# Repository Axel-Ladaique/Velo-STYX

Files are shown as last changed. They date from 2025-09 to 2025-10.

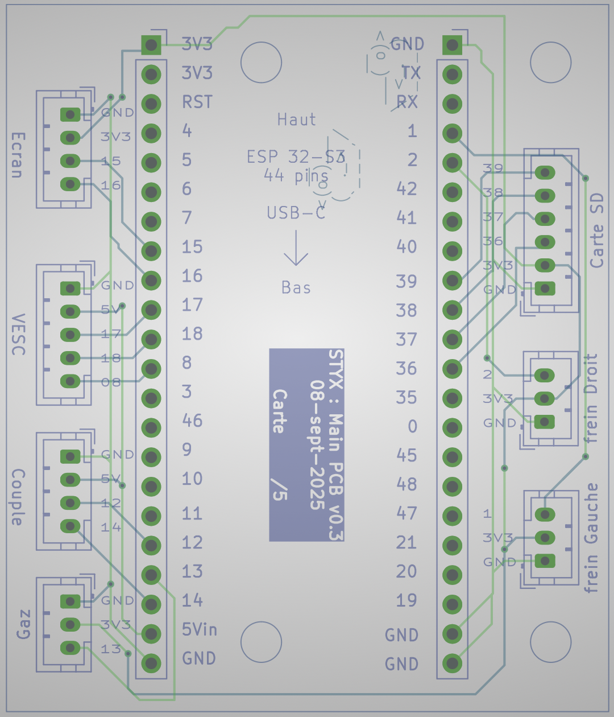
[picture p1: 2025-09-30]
05_Carte PCB/PCB_V0.3_layer_view.png

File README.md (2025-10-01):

# Velo-STYX
Codes et modèles 3D pour s'inspirer ou fabriquer le vélo styx chez soi 
## BOM : Liste des composants
Voici ci dessous la Liste des composants.

[BOM Excel (Original)](https://github.com/Axel-Ladaique/Velo-STYX/blob/main/01_BOM%20Liste%20des%20composants/1_BOM%20STYX%20V2.5.xlsx)

[BOM google sheet](https://docs.google.com/spreadsheets/d/19vOGE_QkLGgu38JTzU2YtKTNE64U9HrzXLUYEj6seYQ/edit?hl=fr&gid=0#gid=0)

Capture d’écran 2025-09-30 à 20 37 25

# Informations concernant les fichiers STEP

- Une fois l’archive décompressée, vous trouverez un fichier au format **.STEP**.  
- Ce fichier contient les modèles 3D présentés ci-dessous :
Capture d’écran 2025-09-22 à 15 25 45

# Fabrication de la carte PCB

Pour fabriquer la carte PCB, il suffit d’envoyer le fichier V0.3 (compressé en .zip) à un fabricant en ligne comme PCBWay. Une fois la commande validée, il faut régler le paiement : petit conseil, choisir la livraison lente revient beaucoup moins cher et reste fiable.
À la réception des cartes, commencez par souder les connecteurs PH2.0, puis les connecteurs JST. Une fois les soudures terminées, insérez l’ESP32 dans le sens indiqué sur la PCB, et la carte est prête à l’emploi.

Ci-dessous, la carte PCB V0.3 : vue de dessus, vue de niveau et vue de dessous.
<p align="left">
  PCB_V0 3_top_view
  PCB_V0 3_layer_view
  PCB_V0 3_bottom_view
</p>

# Marche à suivre pour la roue motorisée
Pour avoir une roue motorisée qui fonctionne avec le freinage régénératif, il nous faut un moteur particulier. Notre moteur doit être un moteur sans roue libre. Pour cela on peut opter pour un moteur direct drive (DD) ou un geared motor. 

## Moteur direct drive (ancienne version mais possible)
Pour la version direct drive, c'est plutôt simple, il suffit d'acheter un moteur direct drive intégré dans une roue arrière de vélo.  
On notera que le moteur direct drive est plus lourd et encombrant. Ce n'est pas la version retenue pour le vélo STYX v2.5 (utilisé dans le vélo STYX V1.0).  
Voici la roue que j'ai utilisée (v1.0) : [Pack Hub moteur roue arrière 26" 36V 500W](https://www.amazon.fr/dp/B0CFFTQTP3?ref=ppx_yo2ov_dt_b_product_details&th=1) 

⚠️ Cette roue est une roue 26" et n'est pas adaptée pour la V2.5 (nombre d'aimants, capteurs hall). Il faudra donc faire des modifications pour adapter une roue de ce type sur la V2.5.  
Cette roue est proposée comme une alternative à la solution geared motor.  

Ci-dessous, la roue avec moteur direct drive sur le vélo STYX V1.0 et le moteur ouvert.  
<p align="left">
  PCB_V0 3_top_view
  PCB_V0 3_layer_view
</p>

## Geared motor (Version Actuelle)
Sur la version 2.5 du vélo STYX, un moteur réducté est utilisé. Cela permet de réduire l'encombrement mais aussi et surtout le poids, c'est pour cela que la plupart des vélos électriques sur le marché sont équipés de ce type de moteur.  
Le moteur réducté est composé d'un moteur électrique entraînant un réducteur planétaire. Ce réducteur réduit la vitesse de rotation mais augmente le couple de sortie.  
Aussi, sur les vélos électriques classiques ce réducteur fait aussi office de roue libre. Cela veut dire que le moteur entraîne la roue dans un sens de rotation mais pas dans l'autre. Cela permet que le moteur entraîne la roue lorsque l'assistance est demandée, mais que lorsque la roue tourne, le moteur n'est pas entraîné. Cela augmente l'efficacité car le moteur génère une traînée électromagnétique lorsqu'il est entraîné.  
Or, dans notre système, nous ne voulons pas avoir de roue libre car notre moteur doit être entraîné par la roue pour faire du freinage régénératif. C'est pour cela que notre moteur doit être modifié par rapport aux moteurs généralement vendus dans le commerce.  

Ci-dessous, des images de porte-satellites avec et sans roue libre.  
<p align="left">
  PCB_V0 3_top_view
  PCB_V0 3_layer_view
</p>

Pour avoir un moteur réducté sans roue libre dans une roue, je suis passé par un fournisseur sur [Alibaba](https://greenpedel.en.alibaba.com/).  
Pour réduire les coûts de frais de port, j'ai commandé le moteur réducté avec la modification pour la roue libre (sans la roue) depuis la Chine puis j'ai commandé une roue motorisée sans modification envoyée depuis l'Europe.  
J'ai fait cette manipulation car je voulais essayer le moteur sans la roue avant de commander le tout avec la roue.  

Voici les prix des différentes options :  

#### Option 1 (testé) :  
  Achat en 2 commandes puis assemblage de la partie modifiée dans la roue (assemblage très simple). Voir les 2 commandes dans [PI fournisseur](https://github.com/Axel-Ladaique/Velo-STYX/tree/main/01_BOM%20Liste%20des%20composants/PI_Fournisseur)  
  + Moteur modifié envoyé de Chine = $45 + $88 = $133 (produit + frais de port = total) [Voir facture moteur](https://github.com/Axel-Ladaique/Velo-STYX/blob/main/01_BOM%20Liste%20des%20composants/PI_Fournisseur/PI_Moteur.pdf)  
  + Roue motorisée (envoyée d'Europe) = $189 (produit + frais de port = total) [Voir facture roue](https://github.com/Axel-Ladaique/Velo-STYX/blob/main/01_BOM%20Liste%20des%20composants/PI_Fournisseur/PI_Moteur.pdf)  
  + Total avec FDP = $322  

  Pour rendre le moteur avec la roue compatible avec la regen, il suffit d'ouvrir le moteur modifié (sans roue), d'en sortir le moyeu moteur (voir photo ci-dessous) et de remplacer le moyeu de la roue motorisée par le moyeu modifié.  
  <p align="left">
    PCB_V0 3_top_view
    PCB_V0 3_layer_view
  </p>

#### Option 2 (pas testée) :  
  Achat en 1 commande (pas testé mais même fournisseur donc mêmes composants)  
  + Moteur modifié avec roue assemblée : $55 + $229 = $284  

#### Option 3 (pas testée) :  
  Achat en 1 commande du moteur modifié  
  + Moteur modifié envoyé de Chine = $45 + $88 = $133 (produit + frais de port = total)  
  + Rayons et jante adaptés (prix = ?)  
  + Assemblage de la roue chez un atelier de vélo local (prix = ?)  

#### Option 4 (pas testée) :  
  Achat en 1 commande de la roue avec le moteur non modifié puis modification du porte-satellite [Voir facture](https://github.com/Axel-Ladaique/Velo-STYX/blob/main/01_BOM%20Liste%20des%20composants/PI_Fournisseur/PI_Roue.pdf)  
  + Roue motorisée avec moteur non modifié : $189 (produit + frais de port = total)  
  + Modification du porte-satellite avec poste à souder [vidéo](https://youtu.be/KDuZFQy_Q-I?si=F1o1J4BLGezd9nKO)

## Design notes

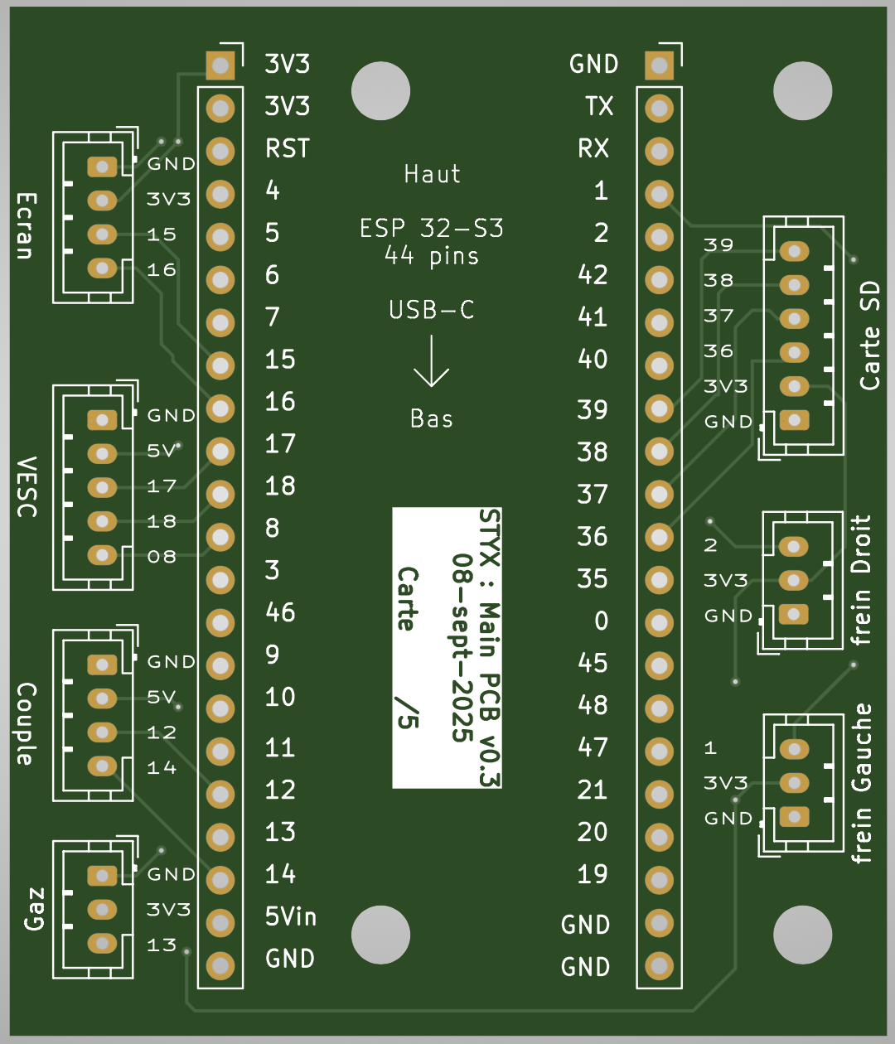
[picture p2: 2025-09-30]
05_Carte PCB/PCB_V0.3_top_view.png

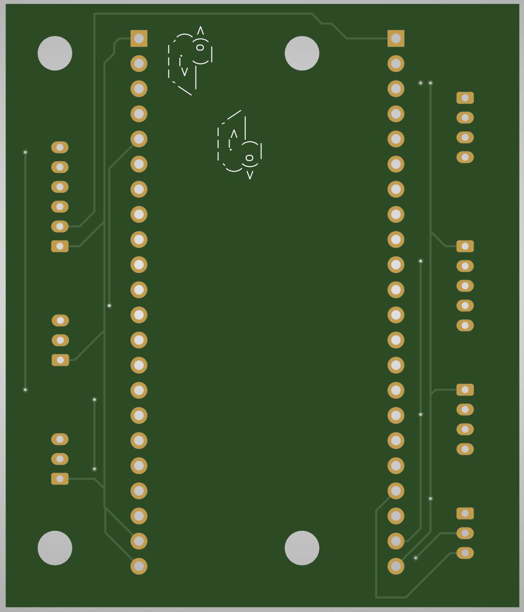
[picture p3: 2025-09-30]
05_Carte PCB/PCB_V0.3_bottom_view.png

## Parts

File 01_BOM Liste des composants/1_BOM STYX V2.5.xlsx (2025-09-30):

Sous système | Item | Commentaire | Lien | Qté | prix unitaire | Total
Vélo STYX complet |  |  |  |  |  | 1560.17 €
Vélo base |  |  |  |  |  | 567.89 € | Sous système | Item | Commentaire | Lien | Qté | prix unitaire | Total
 | TRIBAN RC500 FLATBAR PROWHEEL / SORA | Le vélo doit avoir des frein a disque mecanique (pas d'hydraulique) et un guidon plat | decathlon (https://www.decathlon.fr/p/triban-rc500-flatbar-prowheel-sora/_/R-p-345067) | 1 | 549.00 € | 549.00 € | Outils utiles |  |  |  |  |  | 83.77 €
 | Roue libre PNA 8 vitesses 13/28 | /!\ Roue libre 8 vitesse pour Selecteur 9 vitesse | Beasty-bike (https://www.beastybike.com/cassettes-roues-libres/10396-roue-libre-pna-8-vitesses-13-28.html) | 1 | 18.89 € | 18.89 € |  | Pince à sertir borne à ressort enfichable DuPont SN-2549 | Pour PH2.0 | aliexpress (https://fr.aliexpress.com/item/1005007269635511.html) | 1 | 9.99 € | 9.99 €
Moteur/Roue |  |  |  |  |  | 371.47 € |  | Pince à sertir SN-6 JAW | Pour terminaux UT4-5 | aliexpress (https://fr.aliexpress.com/item/1005008593957205.html) | 1 | 3.79 € | 3.79 €
 | GP-G24R Regen motor only | Moteur avec regen seul (sans la roue) || voir PI pour details | greenpedel-alibaba (https://greenpedel.en.alibaba.com/) | 1 | / | 149.04 € |  | BOITE A OUTILS VELO 900 |  | Decathlon (https://www.decathlon.fr/p/boite-a-outils-velo-900/_/R-p-100427?mc=8381080) | 1 | 69.99 € | 69.99 €
 | GP-G24R Motor-Wheel kit | Moteur sans regen integré dans la roue || voir PI pour details | greenpedel-alibaba (https://greenpedel.en.alibaba.com/) | 1 | / | 207.84 €
 | Câble d'extension de moteur de moyeu Ebike Julet 9 broches (60cm female) |  | aliexpress (https://fr.aliexpress.com/item/1005003749778364.html) | 1 | 14.59 € | 14.59 €
Capteur de couple |  |  |  |  |  | 143.86 € | Plastique pour impression |  |  |  |  |  | 110.96 €
 | Capteur de couple | voir PI pour details | greenpedel-alibaba (https://greenpedel.en.alibaba.com/) | 1 | / | 141.55 € |  | TPU for AMS |  | bambulab (https://eu.store.bambulab.com/fr/products/tpu-for-ams) | 1 | 39.99 € | 39.99 €
 | Connecteur étanche Julet Higo (6 pin Female) |  | aliexpress (https://fr.aliexpress.com/item/1005006444582628.html?gatewayAdapt=glo2fra) | 1 | 2.31 € | 2.31 € |  | ASA |  | bambulab (https://eu.store.bambulab.com/fr/products/asa-filament) | 1 | 24.99 € | 24.99 €
Levier de frein |  |  |  |  |  | 39.58 € |  | PLA Matte |  | bambulab (https://eu.store.bambulab.com/fr/products/pla-matte?id=42996742652123) | 2 | 22.99 € | 45.98 €
 | Ebrake Levers with Analog Output, Left | Envoyé depuis de canada (fraits de port élevés) | ebikes.ca (https://ebikes.ca/ebrake-analog-higo4-left-ls.html) | 1 | 18.00 € | 18.00 €
 | Ebrake Levers with Analog Output, Right | Envoyé depuis de canada (fraits de port élevés) | ebikes.ca (https://ebikes.ca/ebrake-analog-higo4-right.html) | 1 | 18.00 € | 18.00 €
 | Connecteur étanche Julet Higo (4 pin Female) |  | aliexpress (https://fr.aliexpress.com/item/1005006444582628.html?gatewayAdapt=glo2fra) | 2 | 1.79 € | 3.58 €
Ecran GPS |  |  |  |  |  | 45.78 €
 | ESP32 S3 Screen |  | aliexpress (https://fr.aliexpress.com/item/1005006211756061.html) | 1 | 23.39 € | 23.39 €
 | Module GPS |  | aliexpress (https://fr.aliexpress.com/item/1005006494891194.html) | 1 | 19.79 € | 19.79 €
 | Insert M2.5(OD3.5mm)x2.5mm 50pcs | Attention M2.5 (pas M3) | aliexpress (https://fr.aliexpress.com/item/1005003582355741.html) | 1 | 1.66 € | 1.66 €
 | Vis, Class steel, M2.5x4mm 50pcs | Attention M2.5 (pas M3) | aliexpress (https://fr.aliexpress.com/item/32810872544.html) | 1 | 0.94 € | 0.94 €
Pack de condo |  |  |  |  |  | 246.02 €
 | Cellule ultracondensateur 700F 2,7V (interface 2xM5) |  | capcomp (https://shop24.capcomp.de/en/capacitors/ultracap/cells/500f-to-2999f/1123/ultracap-zelle-700f-2-7v-innengewinde-2xm5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) | 20 | 8.89 € | 200.84 €
 | Terminaux cosses à fourche UT4-5 (50 pcs) | besoin de Pince à sertir SN-6 JAW | aliexpress (https://fr.aliexpress.com/item/1005007812607726.html) | 2 | 2.85 € | 5.70 €
 | Carte d'équilibrage de supercondensateur 35mm (2,7V) |  | aliexpress (https://fr.aliexpress.com/item/1005008858296510.html) | 20 | 1.56 € | 31.20 €
 | Stainless Steel, M5 10pcs, 6mm |  | aliexpress (https://fr.aliexpress.com/item/32810872544.html) | 6 | 1.38 € | 8.28 €
Electronique de puissance |  |  |  |  |  | 114.44 €
 | Interupteur 40A |  | aliexpress (https://fr.aliexpress.com/item/1005006290676888.html?curPageLogUid=gCNnFQmCMfqb) | 1 | 1.44 € | 1.44 €
 | FLIPSKY Mini V6 MK5 With Power Button |  | flipsky.net (https://flipsky.net/collections/v6-series/products/mini-v6-mk5-with-power-button) | 1 | 100.00 € | 100.00 €
 | Insert flités M3(OD5) x 5mm | Attention M5 (pas M3) | aliexpress (https://fr.aliexpress.com/item/1005003582355741.html) | 1 | 1.99 € | 1.99 €
 | Câble en Silicone rouge et noir 12AWG (3m) |  | aliexpress (https://fr.aliexpress.com/item/1005007356973020.html) | 1 | 8.99 € | 8.99 €
 | Adaptateur de données mâle vers micro USB femelle à angle droit (V8DO-V8F) |  | aliexpress (https://fr.aliexpress.com/item/1005006553808623.html) | 1 | 2.02 € | 2.02 €
Electronique analyse |  |  |  |  |  | 31.13 €
 | Carte de développement double Type C ESP32-S3 (N16R8 weld) |  | aliexpress (https://fr.aliexpress.com/item/1005005051294262.html) | 1 | 5.39 € | 5.39 €
 | Adaptateur USB C mâle vers femelle, Extension à 90 degrés, 85DD |  | aliexpress (https://fr.aliexpress.com/item/1005004503201824.html) | 1 | 1.29 € | 1.29 €
 | Bande de connecteur JST | Fichier de fabrication en .zip | aliexpress (https://fr.aliexpress.com/item/4000873858801.html) | 1 | 1.69 € | 1.69 €
 | Impression PCB |  | pcbway (https://www.pcbway.fr/) | 1 | 10.00 € | 10.00 €
 | PH2.0 | a verifier | amazon (https://www.amazon.fr/Lyeteung-Connecteur-Broches-Femelle-Pré-Sertis/dp/B0CDG95RDT?__mk_fr_FR=ÅMÅŽÕÑ) | 1 | 11.99 € | 11.99 €
 | Micro SD Card Mini TF Card Reader (Mini SD Card) (https://www.aliexpress.com/item/3256806062285034.html) |  | aliexpress (https://fr.aliexpress.com/item/1005006248599786.html) | 1 | 0.77 € | 0.77 €
Visserie & autres
 | Manchon de câble tressé (5M, Inner Diameter 8mm) |  | aliexpress (https://fr.aliexpress.com/item/1005006219473493.html) | 1 | 4.89 € | 4.89 €
 | Vis, Class steel, M3 | Nombre de vis et hauteur à definir | aliexpress (https://fr.aliexpress.com/item/1005008585550992.html) | 5 | 2.20 € | 11.00 €
 | Insert M3(OD5mm) | Nombre d'insert et hauteur à definir | aliexpress (https://fr.aliexpress.com/item/1005003582355741.html) | 2 | 1.50 € | 3.00 €

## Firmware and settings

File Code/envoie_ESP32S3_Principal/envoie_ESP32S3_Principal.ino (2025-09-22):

/* CODE TEST 20/09/2025 19h15 => Main PCB Envoie Json ESP32S3 --> écran.  échange info Vesc <--> esp32S3 (Main PCB)
//!\\ PCB V0.3
//21/09 Ajout du capteur de cadence
//20/09 Passage en PCB V0.3, changement de pin et lecture du capteur de couple
//13/08 Fix distance + Ajout d’un variateur pour le freinage regeneratif. Test de ralentir automatiquement au dessus de 25km peu concluant
//23/07/2025 Si un fichier existe, creation d'un nouveau fichier pour ne pas ecraser le ficher precedent sur la carte SD 
//20/07/25 Enregistrement des données envoyés par le GPS/ecran. 
//21/06 remise a plat apres les test en I2c et bluetooth car ca ne marchait pas on va ensuite tester de metre le gps sur l’écran.
 Validation => récupère les données du VESC et les envoie sur l’écran. 
 Si le VESC est débranché, envoie des données aléatoires.
 Si VESC rebranché, les données reviennent sur l’écran.

 Validation 2. Recuperation de la valeur du frein et de la gachette des gaz avec envoie sur l'ecran.
 Validation 3 : envoie de la commande au vesc : tunes a revoir mais frein et acceerateur fonctionnent
 22/01 19h30 => Fix distance & vitesse 
 25/01 12h50 => re fix distance, fix calcul d’envoie au vesc 
 25/01 14h40 => changement de la vitesse du serial screen en 115200 Bauds, optimisation du temps d'exectuion de la loop.
 01/02 17h30 => changement sur les envoie de donné au vesc, probleme de multiplicateur réglé.
 07/02 Fix Ah charged/discharged ==> Wh charged Discharged. || fix distance facteur 12,1

Modification du 09/05/2025 pour la nouvelle roue. Changement diamètre, nb poles pour vitesse, 

/* Code écrit par Axel LADAIQUE */
/* Ce code a pour but de traiter et d'envoyer les informations du vélo STYX sur un écran de dev avec ESP32 S3 et une carte SD

Configuration Board => 
- Esp32S3 dev module
- Port Serial (voir problème port/driver)
- Flash Size : 16MB
- Partition scheme : 8M with SPIFF ...
- PSRAM : disable

/ ! \ Arduino IDE v2.3.2 || TFT_eSPI v2.5.43 || esp32 by Espressif v2.0.12
*/

#include <ArduinoJson.h>
#include <HardwareSerial.h>
#include <VescUart.h>

// UART pour la communication avec l'écran
HardwareSerial SerialScreen(1); // UART1 pour l'écran
#define TX_PIN_SCREEN 15 // Pin TX vers le récepteur (écran)
#define RX_PIN_SCREEN 16 // Pin RX (non utilisé ici)

// UART pour la communication avec le VESC
HardwareSerial SerialVESC(2); // UART2 pour le VESC
VescUart vesc; // Objet pour la bibliothèque VESC
#define TX_PIN_VESC 17 // Pin TX pour le VESC
#define RX_PIN_VESC 18 // Pin RX pour le VESC

// Pins supplémentaires pour alimentation et lecture analogique
#define PIN_FREIN_DROIT 2
#define PIN_FREIN_GAUCHE 1
#define PIN_GAZ 13
const int freinInf = 1050;
const int freinSup = 2500;
const int freinInf_G = freinInf;
const int freinSup_G = freinSup;
const int freinInf_D = freinInf;
const int freinSup_D = freinSup;

const int gazInf = 985;
const int gazSup = 3125;


#include <SD.h>
#include <SPI.h>
// Déclaration des pins SPI personnalisées
#define CS_PIN_SD 39
#define MOSI_PIN 38
#define MISO_PIN 36
#define CLK_PIN 37
File dataFile;

#define PIN_COUPLE 12
#define PIN_CANDENCE 14

volatile unsigned long lastPulseMicros = 0;
volatile unsigned long pulseIntervalMicros = 0;
volatile unsigned long pulseCountCad = 0;

float cadenceRPM = 0.0;
const int pulsesPerRevCad = 36;  // nombre d'impulsions par tour (1 aimant = 1 impulsion)
#define WINDOW_MS 500         // Fenêtre pour moyenne glissante
#define TIMEOUT_MS 300        // Timeout sans impulsion pour remettre cadence à 0
#define ALPHA 0.3             // Filtrage exponentiel

float cadenceFiltered = 0;     // Valeur moyenne lissée
unsigned long lastCadenceUpdate = 0;
volatile unsigned long lastPulseTime = 0; // mis à jour dans l'ISR


bool rec = false;
String currentFilename;

String generateUniqueFilename() {
  String baseFilename = "/STYXvelo_P2_AL";
  String extension = ".csv";
  String filename;
  int counter = 1;
  
  // Vérifier si le fichier de base existe
  filename = baseFilename + extension;
  if (!SD.exists(filename)) {
    return filename; // Le fichier de base n'existe pas, on peut l'utiliser
  }
  
  // Chercher un nom de fichier libre avec un numéro
  do {
    filename = baseFilename + "_" + String(counter) + extension;
    counter++;
  } while (SD.exists(filename) && counter < 1000); // Protection contre boucle infinie
  
  return filename;
}

void IRAM_ATTR isr_cadence() {
  unsigned long now = micros();
  unsigned long interval = now - lastPulseMicros;
  if (interval > 20000) { // ignore <20ms (anti-rebond)
    pulseIntervalMicros = interval;
    pulseCountCad++;
    lastPulseMicros = now;
    lastPulseTime = millis(); // <- pour le timeout
  }
}




void setup() {
  // Initialisation des UART
  SerialScreen.begin(115200, SERIAL_8N1, RX_PIN_SCREEN, TX_PIN_SCREEN);
  SerialVESC.begin(115200, SERIAL_8N1, RX_PIN_VESC, TX_PIN_VESC);

  // Association explicite du port série avec l'objet VESC
  vesc.setSerialPort(&SerialVESC);

  // Moniteur série pour le débogage
  Serial.begin(115200);
  delay(1000);



  // Configuration des pins de frein, gaz et couple pour lecture analogique
  pinMode(PIN_FREIN_GAUCHE, INPUT);
  pinMode(PIN_FREIN_DROIT, INPUT);
  pinMode(PIN_GAZ, INPUT);
  pinMode(PIN_COUPLE, INPUT);
  pinMode(PIN_CANDENCE, INPUT_PULLUP);
  attachInterrupt(digitalPinToInterrupt(PIN_CANDENCE), isr_cadence, FALLING);
  analogReadResolution(12);           // Résolution ADC : 12 bits
  analogSetAttenuation(ADC_11db);     // Plage de lecture : 0 à 3.3V

  Serial.println("Émetteur prêt avec :");
  Serial.println("- UART1 : TX=15, RX=16 pour le récepteur (écran)");
  Serial.println("- UART2 : TX=17, RX=18 pour le VESC");

  
  SPI.begin(CLK_PIN, MISO_PIN, MOSI_PIN, CS_PIN_SD);
  // Initialisation de la carte SD
  if (!SD.begin(CS_PIN_SD, SPI)) {
    Serial.println("Erreur : Impossible d'initialiser la carte SD !");
    //while (true);
  }
  Serial.println("Carte SD initialisée avec succès.");

  // Générer un nom de fichier unique
  currentFilename = generateUniqueFilename();
  Serial.println("Nom du fichier : " + currentFilename);
  
  // Ouvrir le fichier pour écriture (crée un nouveau fichier)
  dataFile = SD.open(currentFilename, FILE_WRITE);
  if (dataFile) {
    // Écriture des en-têtes
    dataFile.println("Temps,Tension,Vitesse,GazFrein,WHCharged,WHDischarged,Distance,CurrentIn,MotorCurrent,Lat,Lon,Alt,Vsat,Cap,Sat,HDOP,Heure,Date,Couple,CadenceRPM");
    rec = true;
    dataFile.close();
  } else {
    Serial.println("Erreur : Impossible de créer le fichier " + currentFilename + " !");
    rec = false;
  }

}

float coef_couple = 1.0;
float current_motor;
int lastsd_MS=0;
float vari_vesc = 0;
int nb = 0;
float couple_moy =0;

void loop() {
  int millisdeb = millis();
  nb = nb+1;

  // Lecture des valeurs analogiques
  int frein_G = analogRead(PIN_FREIN_GAUCHE);
  int frein_D = analogRead(PIN_FREIN_DROIT);
  //Serial.print("Valeur frein_G Brute (pin 19) : ");
  //Serial.println(frein_G);
  frein_G = map(frein_G, freinInf_G, freinSup_G, 0, -90);
  //Serial.print("Valeur frein_D Brute (pin 12) : ");
  //Serial.println(frein_D);
  frein_D = map(frein_D, freinInf_D, freinSup_D, 0, -90);
  int frein = frein_G + frein_D;
  if (frein < -90) {frein = -90;}

  int gaz = analogRead(PIN_GAZ);
  //Serial.print("Valeur gaz (pin 20) : ");
  //Serial.println(gaz);
  gaz = map(gaz, gazInf, gazSup, 0, 90);
  float couple = analogRead(PIN_COUPLE);
  Serial.print("couple brut : " );
  Serial.print(couple);
  couple = 0.0267*couple-22.948;
  if (couple<0){
    couple = 0;
  }
  //float cadence = cadenceRPM;
  Serial.print("||  couple : " );
  Serial.print(couple);
  Serial.print(" Nm    nb : " );
  Serial.print(nb);
  couple_moy = (couple_moy+couple);
  Serial.print("   || couple_moy : " );
  Serial.print(couple_moy/nb);
  // Calcul cadence (RPM)
  unsigned long now = millis();
  // Calcul toutes les WINDOW_MS
  if (now - lastCadenceUpdate >= WINDOW_MS) {
      lastCadenceUpdate = now;

      noInterrupts();
      unsigned long pulses = pulseCountCad;   // nombre d’impulsions dans la fenêtre
      pulseCountCad = 0;                       // remise à zéro
      interrupts();

      float cadenceRPM = 0.0;
      if (pulses > 0) {
          float revPerSec = (float)pulses / (float)pulsesPerRevCad / (WINDOW_MS / 1000.0);
          cadenceRPM = revPerSec * 60.0;
      }

      // Timeout si plus d’impulsion depuis TIMEOUT_MS
      if (now - lastPulseTime > TIMEOUT_MS) {
          cadenceRPM = 0.0;
      }

      // Filtrage exponentiel pour lisser
      cadenceFiltered = (1 - ALPHA) * cadenceFiltered + ALPHA * cadenceRPM;

      Serial.print("Cadence filtrée (RPM) : ");
      Serial.println(cadenceFiltered);
  }
  //delay(1000);
  // Affichage des valeurs analogiques
  /*Serial.print("Valeur frein (pin 12) : ");
  Serial.println(frein);
  Serial.print("Valeur gaz (pin 14) : ");
  Serial.println(gaz);*/
  float gazfrein = 0;
  if (gaz>90){gaz=90;}
  
  if (frein<0) {gazfrein=frein;}
  else {
    if (gaz <0){gazfrein=0;}
    else{gazfrein=gaz;}
  }

  //Serial.println( "temps gazfrein : " + String (millis() - millisdeb));
  //Serial.print("Valeur gazFREIN : ");
  //Serial.println(gazfrein);

  // Préparation des données JSON
  StaticJsonDocument<500> doc;

  doc["Gaz/frein"] = gazfrein;
  doc["Temps seconde"] = millis() / 1000.0;

  float vitesse = 0;

  if (vesc.getVescValues()) {
    // Lecture des valeurs du VESC
    //Serial.println("Vesc");
    doc["Tension"] = vesc.data.inpVoltage;
    float rpm = vesc.data.rpm/10;                         // The ’10’ is the number of pole pairs in the motor. the motors have 52 poles, therefore 26 pole pairs
    vitesse = rpm*60*PI*(28*0.0254)/(1000)/4.4;       //vitesse en Km/h
    //Serial.println("RPM :" + String(rpm) + "vitesse :" + String(vitesse));
    doc["Vitesse"] = vitesse; // Convertir RPM en vitesse
    doc["WHcharged"] = vesc.data.wattHoursCharged;
    doc["WHdischarged"] = vesc.data.wattHours;
    float tach = vesc.data.tachometer/(20*3);           // The '52' is the number of motor poles multiplied by 3 (3hall sensor I think)
    //Serial.println ("tach : " + String(tach));
    float distance = tach*3.142*(0.001)*(28.0*0.0254)/4.4;       // 3.142*(0.0001)*(26.0*0.0254) //26*0.0254 = diametre de la roue (26 pouces *0,0254). Je ne sais pas pk *12.1
    doc["Distance"] = distance;
    //Serial.println ("Disatnce : " + String(distance));
    doc["Current_in"] = vesc.data.avgInputCurrent;
    doc["Message"] = "VESC_OK";
  } else {
    Serial.println("pas vesc");
    doc["Tension"] = 99.99;
    doc["Vitesse"] = 99.9; // Convertir RPM en vitesse
    doc["WHcharged"] = 99.99;
    doc["WHdischarged"] = 99.99;
    doc["Distance"] = 999.99;
    doc["Current_in"] = 99.99;
    // En cas d'échec de lecture du VESC
    doc["Message"] = "VESC_NOK";
  }
  current_motor=vesc.data.avgMotorCurrent;
  doc["Rec"] = rec;
  //Serial.println("doc Rec" + String(rec));
  // Sérialisation des données JSON
  String jsonOutput;
  serializeJson(doc, jsonOutput);

  //Serial.println( "temps json+infovesc : " + String (millis() - millisdeb));

  // Envoi des données JSON via UART (écran)
  SerialScreen.println(jsonOutput);
  //Serial.println("Longueur de jsonOutput : " + String(jsonOutput.length()));

  //Serial.println( "temps send ecran : " + String (millis() - millisdeb));

  // Affichage pour le débogage
  //Serial.println("Données envoyées :");
  //Serial.println(jsonOutput);

  // Enregistrer les données dans un fichier CSV
  if (vesc.getVescValues()) {
    if (millis()-lastsd_MS>500){
      if (rec==true){
      
        Serial.println("if milis + rec ");
        if (SerialScreen.available()) {
          Serial.println("serial screen");
          // Lecture de la chaîne JSON envoyée
          String receivedData = SerialScreen.readStringUntil('\n');
          receivedData.trim(); // Supprime les espaces ou retours à la ligne en début et fin de chaîne

          // Affiche la chaîne brute reçue pour débogage
          Serial.print("Données reçues brutes : ");
          Serial.println(receivedData);

          // Parse le JSON reçu
          StaticJsonDocument<256> doc_gps;
          DeserializationError error = deserializeJson(doc_gps, receivedData);

          if (error) {
            Serial.print(F("Erreur de parsing JSON: "));
            Serial.println(error.c_str());
            return;
          }

          // Récupérer les champs du JSON GPS
          float latitude     = doc_gps["lat"];       // Latitude (Float)
          float longitude    = doc_gps["lon"];     // Longitude (Float)
          float altitude     = doc_gps["alt"];     // Altitude (Float)
          float vitesse_sat  = doc_gps["spd"];     // Vitesse satellite (Float)
          float cap          = doc_gps["hdg"];     // Cap (Float)
          int satellites     = doc_gps["sat"];     // Nombre de satellites (Int)
          float hdop         = doc_gps["hdop"];    // Précision horizontale (Float)
          unsigned long heure_GMT = doc_gps["tim"]; // Heure brute GMT (ULong)
          unsigned long date       = doc_gps["dat"]; // Date brute (ULong)

          // Affichage des données GPS pour débogage
          Serial.println("Données GPS reçues et parsées :");
          Serial.print("Latitude : "); Serial.println(latitude, 6);
          Serial.print("Longitude : "); Serial.println(longitude, 6);
          Serial.print("Altitude (m) : "); Serial.println(altitude);
          Serial.print("Vitesse satellite (km/h) : "); Serial.println(vitesse_sat);
          Serial.print("Cap (°) : "); Serial.println(cap);
          Serial.print("Satellites : "); Serial.println(satellites);
          Serial.print("HDOP : "); Serial.println(hdop);
          Serial.print("Heure GMT brute : "); Serial.println(heure_GMT);
          Serial.print("Date brute : "); Serial.println(date);

          dataFile = SD.open(currentFilename, FILE_APPEND);
          if (dataFile) {
            rec=true;
            dataFile.print(doc["Temps seconde"].as<float>());
            dataFile.print(",");
            dataFile.print(doc["Tension"].as<float>());
            dataFile.print(",");
            dataFile.print(doc["Vitesse"].as<float>());
            dataFile.print(",");
            dataFile.print(doc["Gaz/frein"].as<float>());
            dataFile.print(",");
            dataFile.print(doc["WHcharged"].as<float>());
            dataFile.print(",");
            dataFile.print(doc["WHdischarged"].as<float>());
            dataFile.print(",");
            dataFile.print(doc["Distance"].as<float>());
            dataFile.print(",");
            dataFile.print(doc["Current_in"].as<float>());
            dataFile.print(",");
            dataFile.print(current_motor);
            dataFile.print(",");
            dataFile.print(doc_gps["lat"].as<float>(),6);
            dataFile.print(",");
            dataFile.print(doc_gps["lon"].as<float>(),6);
            dataFile.print(",");
            dataFile.print(doc_gps["alt"].as<float>());
            dataFile.print(",");
            dataFile.print(doc_gps["spd"].as<float>());
            dataFile.print(",");
            dataFile.print(doc_gps["hdg"].as<float>());
            dataFile.print(",");
            dataFile.print(doc_gps["sat"].as<int>());
            dataFile.print(",");
            dataFile.print(doc_gps["hdop"].as<float>());
            dataFile.print(",");
            dataFile.print(doc_gps["tim"].as<unsigned long>());
            dataFile.print(",");
            dataFile.print(doc_gps["dat"].as<unsigned long>());
            dataFile.print(",");
            dataFile.print(couple_moy/nb);
            dataFile.print(",");
            dataFile.println(cadenceFiltered);
            dataFile.close();
          } else {
            rec=false;
          //Serial.println("Erreur : Impossible d'écrire dans le fichier datalog.csv !");
          } 
        }
      } 
      nb = 0;
      couple_moy =0;
      lastsd_MS=millis();
    }
  }

    //Serial.println( "temps sd : " + String (millis() - millisdeb));
  //-------------------------------------------------------------------------------------------
  //Envoie de données au Vesc 
  float comVesc = 0;
  comVesc = gazfrein/90;  //remet entre -1 et 1
  
  //Serial.println("comVesc avant : " + String(comVesc));
  //Serial.println("comvesc" + String(comVesc));
  if (comVesc<-0.1){
    if (vari_vesc>(comVesc*25)){
      vari_vesc = vari_vesc - 0.4;  
    }else{
      vari_vesc=comVesc*25;
    }
    vesc.setBrakeCurrent(vari_vesc); // entre 0 et -25A
  }
  Serial.print("vari_vesc : ");
  Serial.println(vari_vesc);
  Serial.print("comvesc *25 : ");
  Serial.println(comVesc*25);

  if (comVesc>0.1){
    vari_vesc = 0;
    comVesc=comVesc*15;
    vesc.setCurrent(comVesc);        //entre 0 et 20A
    
  }
  if (vitesse>25){
    vesc.setRPM(820); //820 RPM <=> 25 km/h
    Serial.print("au dessus de 25km/h : ");
    Serial.println(vitesse);
    comVesc=0;
  }
  if (comVesc>-0.1 && comVesc<0.1){ 
    comVesc=0; 
    vari_vesc = 0;
    vesc.setCurrent(comVesc);
  }

  //Serial.println( "temps fin : " + String (millis() - millisdeb));
  
  //Serial.println("comVesc apres : " + String(comVesc));
  


  //-------------------------------------------------------------------------------------------


  //delay(40); // Pause avant prochaine boucle
  //delay(2000);
}

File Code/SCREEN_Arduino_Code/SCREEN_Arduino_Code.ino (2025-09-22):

//CODE FONTIONEL 20/07 16h30 => Affichage sur ecran + réception Json ESP32S3
//20/07 Fix transmission/Enregistrement des données GPS. Fix affichage vitesse et attfichage début.
//16/07 ajout du gps A essayer avec le reste du vélo (verifier l'envoie des données gps lors de l'envoie/reception de la commande message = "____GPS")
//21/06 remise a plat apres les test I2C et bleutooth car ca ne fonctionne pas. 
// 16_16/03 16h40 ===> correction aute orthographe + 1pxl jauges
//fix de la jauge de droite (mtn dans le bon sens)
//Ajout page de demarrage 
//fix distance et rec
//Fix serial 115200
//preparation touch screen (touch screen ready
//toucher pour passer validé

/* Code écrit par Axel LADAIQUE */
/*Ce code a pour but d'afficher les informations reçues du vélo STYX sur une carte de dev avec esp32 S3

Configuration Board => 
-Esp32S3 dev module
-Port Serial(voir problème port/driver)
-Flash Size : 16MB
-Partition scheme : 16M Flash (3MB APP/9.9MB FATFS)
-PSRAM : QSPI PSRAM

/ ! \ voir dans le dossier la librairie qui fonctionne avec les modifications déjà effectuées.

/ ! \ Arduino IDE v2.3.2 || TFT_eSPI v2.5.43 || esp32 by Espressif v2.0.12
*/


#include <TFT_eSPI.h>  // Inclure la bibliothèque TFT_eSPI
#include "LOGO_V1_240x240.h"
#include "CST816S.h"
#include "Image_FOND_240x240.h"
TFT_eSPI tft = TFT_eSPI();  // Création de l'objet pour l'écran
TFT_eSprite imgFond = TFT_eSprite (&tft);
TFT_eSprite speed = TFT_eSprite (&tft);
TFT_eSprite spriteJauge = TFT_eSprite (&tft);
TFT_eSprite spriteTension = TFT_eSprite (&tft);
#include <ArduinoJson.h>
#include <HardwareSerial.h>

HardwareSerial mySerial(1);  // Utilise UART1

CST816S touch(6, 7, 13, 5); // sda, scl, rst, irq           //----------------------------------------------------------------------------------------------

#include <TinyGPS++.h>
#define GPS_RX_PIN 15
#define GPS_TX_PIN 16
HardwareSerial SerialGPS(2);
TinyGPSPlus gps;


void setup() {
  
  Serial.begin(115200);
  delay(1000);  // Attente que la communication série soit prête
  SerialGPS.begin(115200, SERIAL_8N1, GPS_RX_PIN, GPS_TX_PIN);  // UART GPS

  Serial.println("Attente des données GPS...");

  tft.init();              // Initialiser l'écran
  tft.setRotation(2);      // Définir l'orientation (1 pour horizontal, ajuster si besoin)
  tft.fillScreen(TFT_WHITE); // Remplir l'écran en blanc

  tft.setSwapBytes(true);
  tft.pushImage (0,0, 240, 240, LOGO_V1_240x240);    
  imgFond.createSprite(240, 240);
  speed.createSprite(120,80);
  spriteJauge.createSprite(240,240);
  spriteTension.createSprite(30,10);
  imgFond.setSwapBytes(true);
  imgFond.setColorDepth(8);
  tft.setTextColor(TFT_BLACK);
  mySerial.begin(115200, SERIAL_8N1, 17, 18);  // Configurer les pins pour UART1
  
  
  Serial.println("Récepteur prêt.");
  touch.begin();                                 //----------------------------------------------------------------------------------------------

  
  if (true){
    int y=0;
    while (y>-50){
      
      tft.pushImage (0,y, 240, 240, LOGO_V1_240x240);
      y--;
      if (y>-5){delay(60);}
      if (y>-10){delay(30);}
      if (y>-20){delay(10);}
      if (y<-30){delay(10);}
      if (y<-40){delay(30);}
      if (y<-45){delay(60);}
      delay(10);
      if (touch.available()) {
        if (touch.data.y > 0) { // Si la position Y est dans la zone souhaitée
          Serial.println("Écran touché ! Quitte la boucle.");
          break; // Quitter la boucle
        }
      }
    }
    
    //tft.drawString("! Attention ! " ,30, 102, 4);
    tft.drawString("Ce velo est un prototype en cours " ,5, 95, 2);
    tft.drawString("de developpement Le frein moteur" ,3, 110, 2);
    tft.drawString("recharge les supercondensateurs." ,5, 125, 2);
    tft.setTextColor(TFT_RED);
    tft.drawString("Attention : T < 50 V !" ,10, 145, 4);
    //tft.drawString("Ne pas depasser 35 V !" ,10, 140, 2);
    //tft.drawString("Faire attention lors de l'utilisation" ,15, 155, 2);
    tft.setTextColor(TFT_BLACK);
    tft.drawString("Bonne route !" ,25, 170, 2);
    tft.drawString("Prototype 2 - Axel Ladaique" ,33, 185, 2);
    tft.drawString("  Juil. 2025" ,82, 223, 1);
    tft.drawString ("Toucher pour passer", 63, 210, 1);
    
    unsigned long startTime = millis(); // Temps de début
    const unsigned long maxDelay = 30000; // Délai maximum de 15 secondes (en millisecondes)

    while (true) {
        // Si l'écran est touché
        if (touch.available()) {
            if (touch.data.y > 0) { // Si la position Y est dans la zone souhaitée
                Serial.println("Écran touché ! Quitte la boucle.");
                break; // Quitter la boucle
            }
        }

        // Vérifie si 15 secondes se sont écoulées
        if (millis() - startTime >= maxDelay) {
            Serial.println("15 secondes se sont écoulées, fin de la boucle.");
            break; // Quitter la boucle après 15 secondes
        }

        delay(50); // Pause pour éviter une surcharge CPU
    }

  }
  
  
  
  //tft.pushImage (0,0, 240, 240, Image_FOND_240x240) ;

}
float x=0;
int angleDeb = 45;    //45  Angle du Bas
int angleFin = 135;   //135 Angle du Haut
float angleJauge = 0;

float tension = 0;           // Tension (Float)
float vitesse = 0;           // Vitesse (Float)
float gazFrein = 0;        // Gaz/frein (Float)
float whCharged = 0;       // WHcharged (Float)
float whDischarged = 0; // WHdischarged (Float)
float tempsSeconde = 0;// Temps seconde (Float)
float distance = 0;         // Distance (Float)
bool rec = false;                    // Rec (Bool)
float currentIn = 0;      // Current_in (Float)
const char* message = "";     // Message (String)
String currentIn_str = "";

String getGPSJson() {
  StaticJsonDocument<256> doc;

  doc["lat"]  = gps.location.lat();
  doc["lon"]  = gps.location.lng();
  doc["alt"]  = gps.altitude.meters();
  doc["spd"]  = gps.speed.kmph();          // vitesse en km/h
  doc["hdg"]  = gps.course.deg();          // cap en degrés
  doc["sat"]  = gps.satellites.value();    // nb de satellites
  doc["hdop"] = gps.hdop.hdop();           // précision horizontale
  doc["tim"]  = gps.time.value();          // ex: 11325600 pour 11:32:56.00
  doc["dat"]  = gps.date.value();          // ex: 160725 pour 16/07/2025

  String output;
  serializeJson(doc, output);
  return output;
}
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
